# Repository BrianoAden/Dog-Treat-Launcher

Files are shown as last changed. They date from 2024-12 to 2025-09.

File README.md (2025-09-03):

<h1>Dog Treat Dispenser</h1>
<p> This project was for my EDES 301 class. Following is a link to the Hackster.io page I put up detailing the physical build of my project.</p>
<a href="https://www.hackster.io/aden-briano/edes301-dog-treat-launcher-bcfb15">Dog Treat Launcher</a>
<p> Now, I will walk you through the software build required to run this project!</p> 

<h2> Setup </h2>
<p> You are going to need to install the operating system on your PocketBeagle. You will need an SD card and SD card flashing software, like Etcher. 
Download bone-debian-10.11-iot-armhf-2022-02-03-4gb.img.xz from <a href="https://rcn-ee.com/rootfs/bb.org/testing/2022-02-03/buster-iot/">OS</a>. 
Use Etcher to flash your SD card. You can now insert your SD card into your PocketBeagle and plug your PocketBeagle into your laptop. 
Great! Now we can get started. You will need to use the Cloud9 IDE to code on the PocketBeagle using Python. Navigate to http://192.168.6.2:3000/ 
in your browser if you're on mac, or http://192.168.7.2:3000/ if you're on windows. You will also need your Beagle to be connected to the internet for this project. 
There are online resources on how to do this, so I won't walk through it. Once you're on Cloud9, run the following commands.</p>
<p>
                                            $ sudo apt-get update <br>
                                            $ sudo apt-get install build-essential python-dev python-setuptools python-smbus -y <br>
                                            $ sudo apt-get install python-pip python3-pip -y <br>
                                            $ sudo apt-get install zip -y <br>
                                            $ sudo pip3 install --upgrade setuptools <br>
                                            $ sudo pip3 install --upgrade Adafruit_BBIO <br>
                                            $ sudo pip3 install adafruit-blinka <br>
</p>
<p>
Now copy this github repo onto your PocketBeagle using the following command <br>
                                            $ git clone https://github.com/BrianoAden/EDES301 <br>
<h2> Package Installation </h2>
In order to run our project, we need to install the following packages: SpeechRecognition, PyAudio. <br> Let's begin the installation process. Run the following commands. <br>
<br>
$ sudo apt-get update <br>
$ sudo apt-get install -y swig libpulse-dev libasound2-dev <br>
$ sudo apt-get install libportaudio0 libportaudio2 libportaudiocpp0 portaudio19-dev <br>
$ sudo apt-get python-dev <br>
$ sudo python pyaudio/setup.py install <br>
$ sudo python3 -m pip install SpeechRecognition==3.9.0 <br>
<br>

Plug in your USB microphone. Let's check if it's recognized by the PocketBeagle. Run the following command. <br>
$ arecord -l <br>
You should see the following in your output. <br>
<br>
card 1: Device [USB PnP Sound Device], device 0: USB Audio [USB Audio] <br>
  Subdevices: 1/1 <br>
  Subdevice #0: subdevice #0 <br>
<br>
Good, our microphone is almost ready! We just need to set it as our default device. Run the following command. <br>
<br>
$ nano ~/.asoundrc <br>
<br>
Now write in the following. <br>

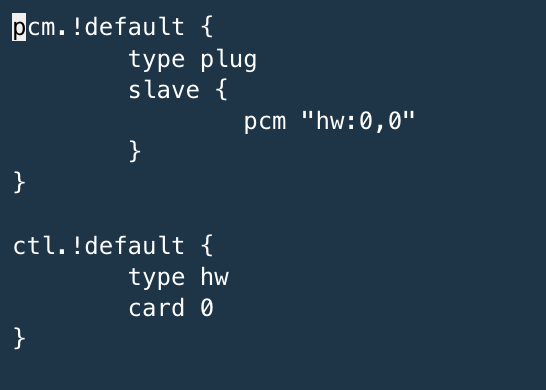
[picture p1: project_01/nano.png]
nano image
 <br>

Redundancy is resiliency, so run this just to be safe. <br>
$ sudo apt-get install -y python-pyaudio python3-pyaudio <br>

Now we should be good to go!
</p>
<h2> Software Operation </h2>
Note! You are required to be connected to the internet to run this project, as the recognize_google() method used by SpeechRecognition requires the internet.
If you manage to connect to the internet through your laptop, but when you reboot your PocketBeagle it disconnects, try running the following commands. <br>
<br>
$ sudo dhclient usb1 <br>
<br>
It's going to ask for a password. The password is temppwd. <br>
If you want to run the program, type sudo ./run into your terminal while in the treat_launcher directory. If this doesn't work, run chmod 755 ./run
to make it executable. To auto-run on boot, perform the following. <br>
<br>
$ sudo crontab -e <br>
<br>
Write the following at the bottom of the file <br>
<br>
@reboot sleep 30 && bash /var/lib/cloud9/EDES301/project_01/python/treat_launcher/run > /var/lib/cloud9/logs/cronlog 2>&1<br>
<br>
Now reboot and it should be good! Run the following to kill the processes. <br>
<br>
$ ps -ef <br>
$ sudo kill -9 (process id(s)) <br>
<br>
Now, you should be set to run the project. In each file under EDES301/project_01/python, there are tests you can use to debug a component.
I hope everything goes well, and I hope your dog loves it! Good luck building!

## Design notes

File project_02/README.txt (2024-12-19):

Dog Treat Launcher PCB

You want to manufacture this PCB??? Wow you must really love your dog! Or you're just curious and wanted to read this file. Well, in the folder that you found this README inside, "project_02", there are three folders. Inside docs are just some screenshots of different parts of the board. Inside EAGLE, you will find the library I used to create the board, as well as the board's schematic and brd file. Inside MFG are the gerber files that you can use if you feel like spending a pretty penny on manufacturing this board. 
This board is designed after the Dog Treat Launcher I designed and developed in project_01. If you care to learn more about that project, please read the README file in project_01. Following is the link to the hackster page I put up for the project. https://www.hackster.io/aden-briano/edes301-dog-treat-launcher-bcfb15 Enjoy!

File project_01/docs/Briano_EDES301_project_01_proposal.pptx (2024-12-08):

## EDES 301 Dog Treat Dispenser

12/05/2024
Aden Briano

## Background Information

  - Inspiration: Dog Treat Dispenser W/Arduino (https://www.sciencebuddies.org/science-fair-projects/project-ideas/Elec_p106/electricity-electronics/automatic-dog-treat-dispenser)
  - Packages to use: Adafruit_BBIO (https://pypi.org/project/Adafruit-BBIO/), SpeechRecognition (https://github.com/Uberi/speech_recognition/blob/master/reference/library-reference.rst), PyAudio (https://github.com/CristiFati/pyaudio)
Is your dog tired of having to sit or lie down to receive a treat? Do they want something more stimulating? Well I’ve got them covered! I’m going to make a treat dispenser box with a flywheel launcher and treat feeder mechanism lying on top. In front of the box there will be a large blue button and a large yellow button with a same colored LED above, embedded into the wall of the box. When the human gives the “Start the game” command, a random LED will light up, and the dog is required to press the corresponding button in 10 seconds to launch a treat (which they can then chase after). The box will need to receive the command again to restart the process. The Dispenser will use an IR sensor to detect if the feeding tube is out of treats, and buzz loudly when it needs to be refilled.

## Github Repository and Hackster.io Post

Dog Treat Launcher (https://www.hackster.io/aden-briano/edes301-dog-treat-launcher-bcfb15)
EDES301 Github (https://github.com/BrianoAden/EDES301)

## System Block Diagram

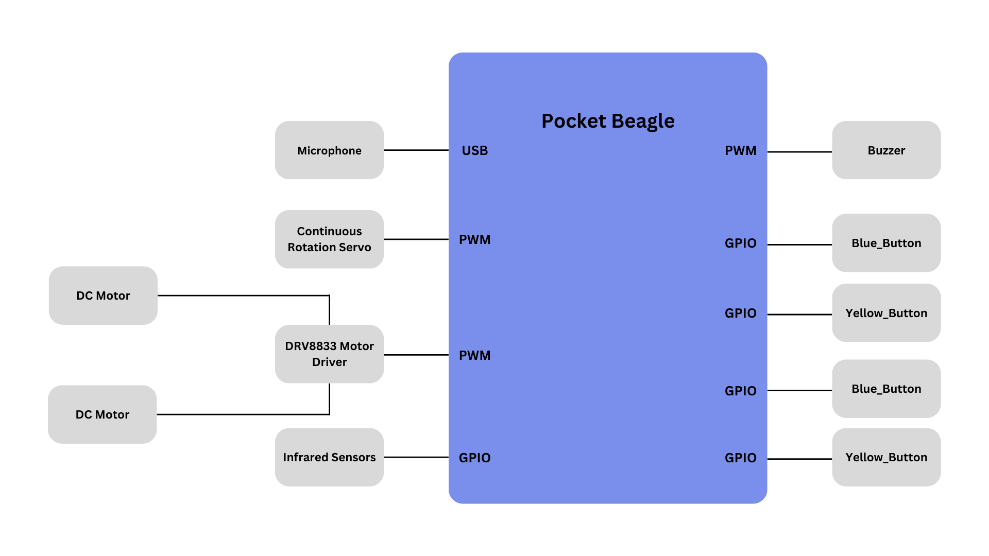
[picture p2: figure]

## Power Block Diagram

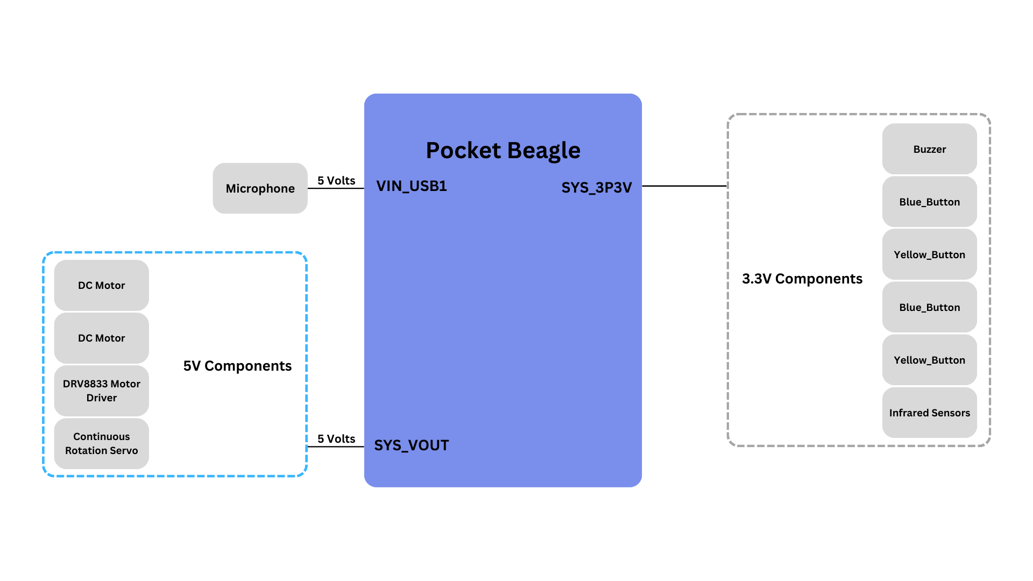
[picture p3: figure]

## Software Framework Diagram

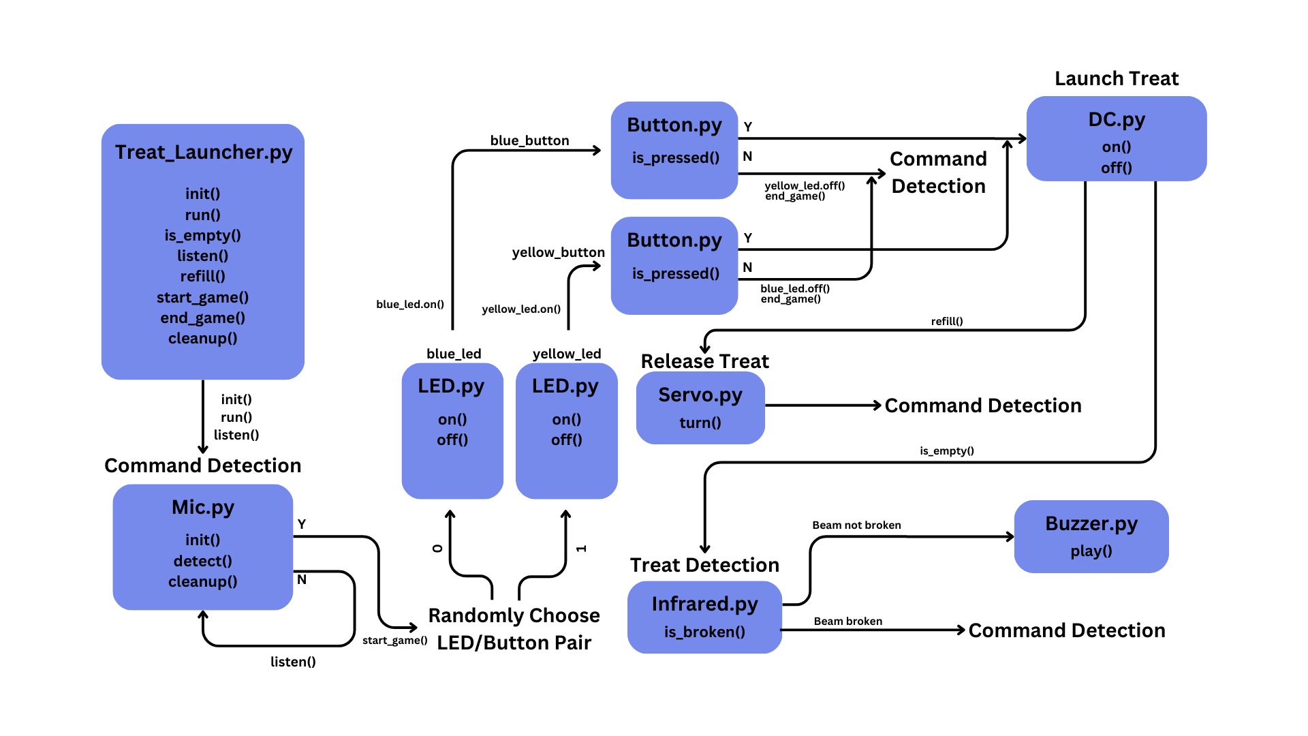
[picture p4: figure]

## Components / Budget

Component | EDES301 to Buy? | Cost
Continuous Rotation Motors (https://www.amazon.com/FEETECH-Continuous-Rotation-Matching-Helicopter/dp/B0B42KLJ9G?th=1) | Yes | $26.99
L298N Motor Driver (https://www.amazon.com/Qunqi-Controller-Module-Stepper-Arduino/dp/B014KMHSW6) | Yes | $6.99
Blue and Yellow Button (https://www.adafruit.com/product/1186) | No | $20
USB Microphone (https://www.amazon.com/gp/product/B01MQ2AA0X) | No | $7.96
Buzzer | No | N/A
DC Motors (https://www.amazon.com/EUDAX-Electric-Magnetic-Propeller-Connector/dp/B08GPPJR1T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) | No | $11.99
Rigid Clear Acrylic Pipe (https://www.amazon.com/MECCANIXITY-Acrylic-Lanterns-Cooling-System/dp/B0B6QFJCLZ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) | No | $14.14
IR Sensor (https://www.electromaker.io/shop/product/ir-break-beam-sensor-3mm-leds?gad_source=1) | No | $9.99
Yellow and Blue LEDS | No | N/A

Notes: Need DC motors for flywheel mechanism. Continuous rotation servo for feeding mechanism.

How do I know when the treats are empty? How will I alert the user?
When do I stop dispensing treats?
Finalize BOM

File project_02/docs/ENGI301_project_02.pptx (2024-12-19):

## EDES 301 PCB Project

Aden Briano
Due 12/17/2024 @ 11:59pm

## Project Options

- Can choose one of two options:
  1. Create a PCB based on your Project #1
  2. Create a PCB based on an example project
- See Project #2 assignment for specific details
  - If choosing Option 1
    - Replace Background Information and System Block Diagram slides with your slides from the Project #1 proposal
    - Create a Mechanical Drawing
  - If choosing Option 2
    - Used provided Background Information and System Block Diagram slides
    - Create a Mechanical Drawing

Remove this slide in your submission

## Background Information

- Hardware:
  - Two DC Motors
  - SG90 Servo
  - IR Break Beam Sensor
  - Two Buttons and Two LEDS (Blue, Yellow)
  - USB Microphone
  - Buzzer
- Software:
  - Adafruit_BBIO (https://pypi.org/project/Adafruit-BBIO/)
  - SpeechRecognition (https://github.com/Uberi/speech_recognition/blob/master/reference/library-reference.rst)
  - PyAudio (https://github.com/CristiFati/pyaudio)

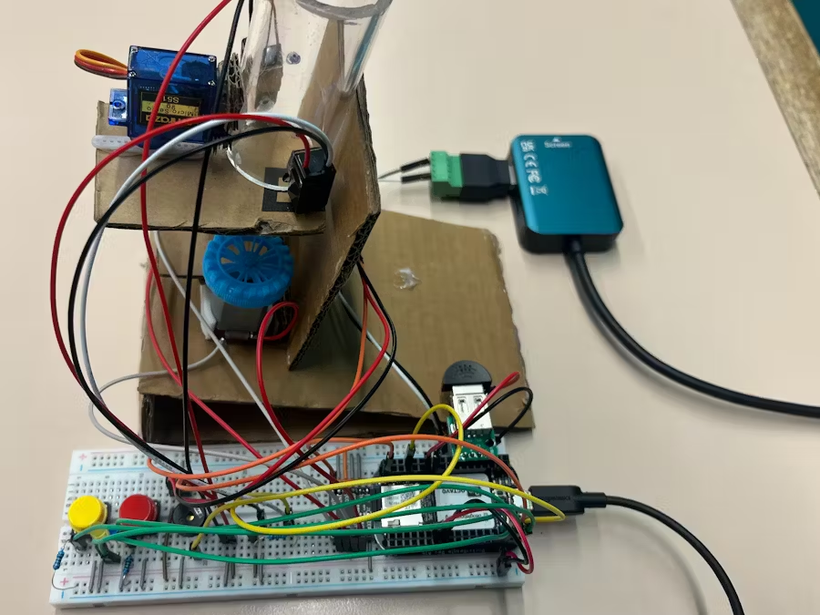
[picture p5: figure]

## System Block Diagram – Dog Treat Launcher

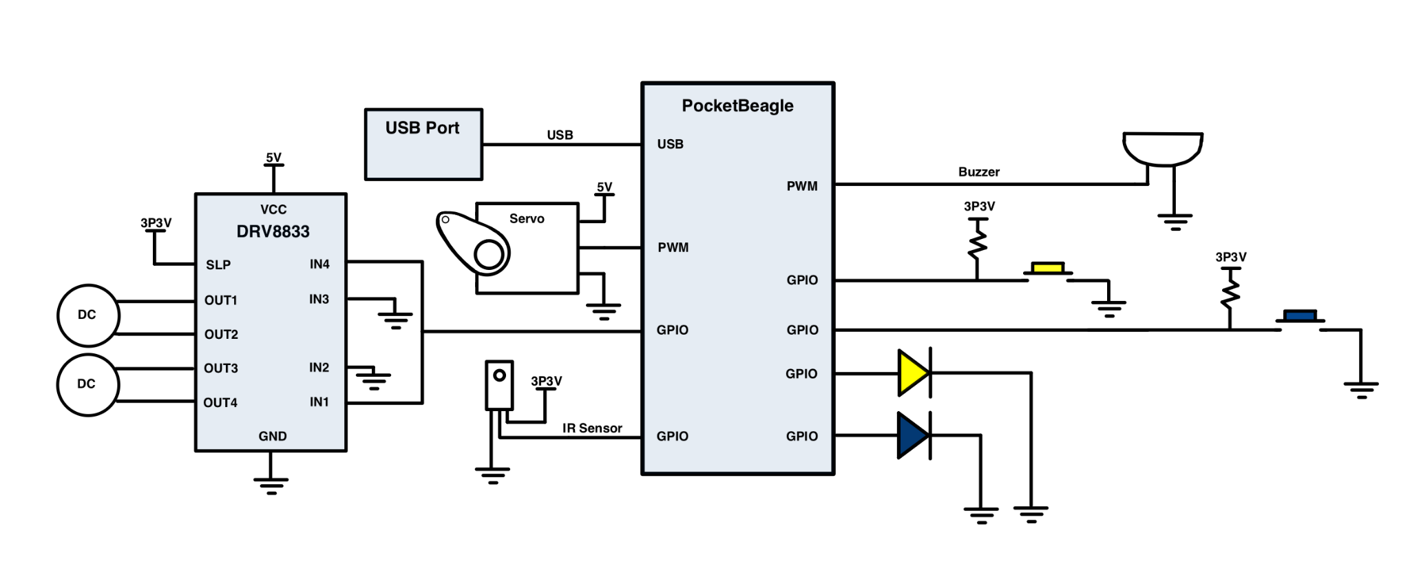
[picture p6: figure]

## Mechanical Drawing

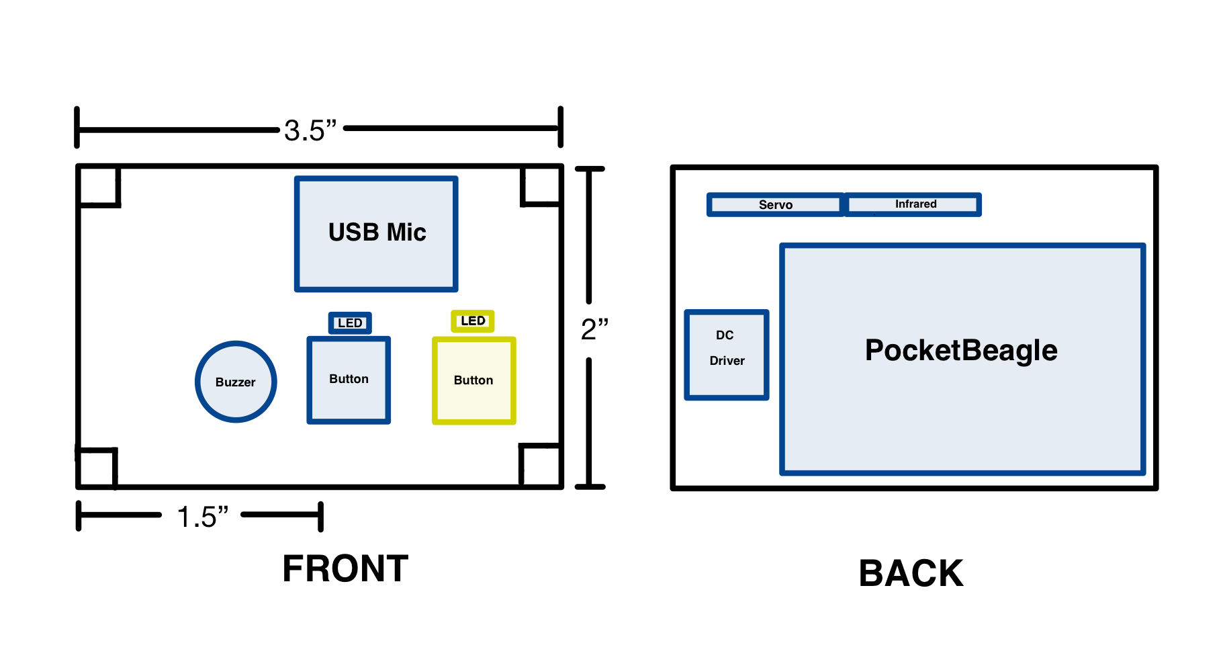
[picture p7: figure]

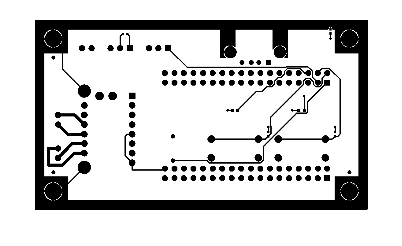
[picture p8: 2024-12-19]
project_02/docs/Top_Layer_Photos/Top_Copper.png

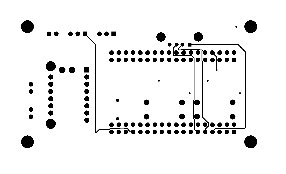
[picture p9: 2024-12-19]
project_02/docs/Bottom_Layer_Photos/Bottom_Copper.png

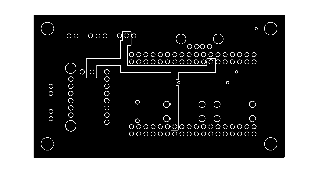
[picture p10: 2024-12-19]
project_02/docs/Top_Layer_Photos/Copper_Layer_15.png

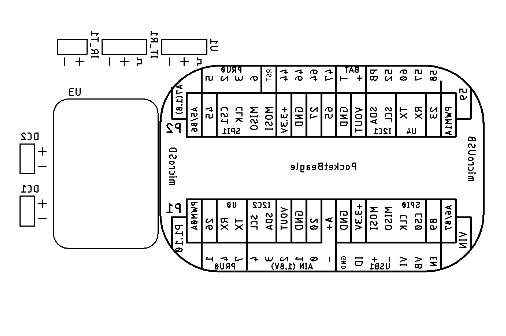
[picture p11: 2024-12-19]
project_02/docs/Bottom_Layer_Photos/Silkscreen_Bottom.png

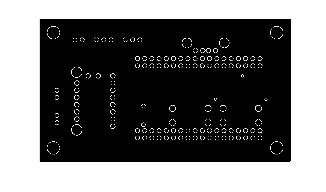
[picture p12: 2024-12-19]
project_02/docs/Top_Layer_Photos/Copper_Layer_2.png

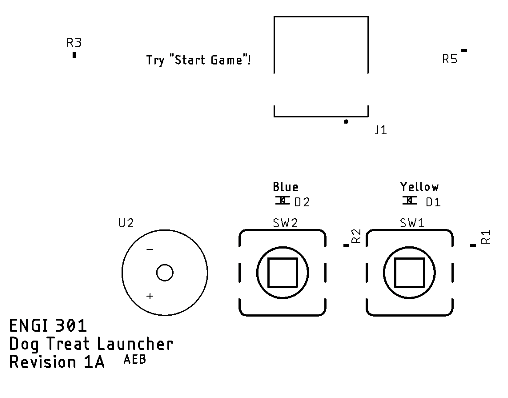
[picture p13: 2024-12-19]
project_02/docs/Top_Layer_Photos/Silkscreen_Top.png

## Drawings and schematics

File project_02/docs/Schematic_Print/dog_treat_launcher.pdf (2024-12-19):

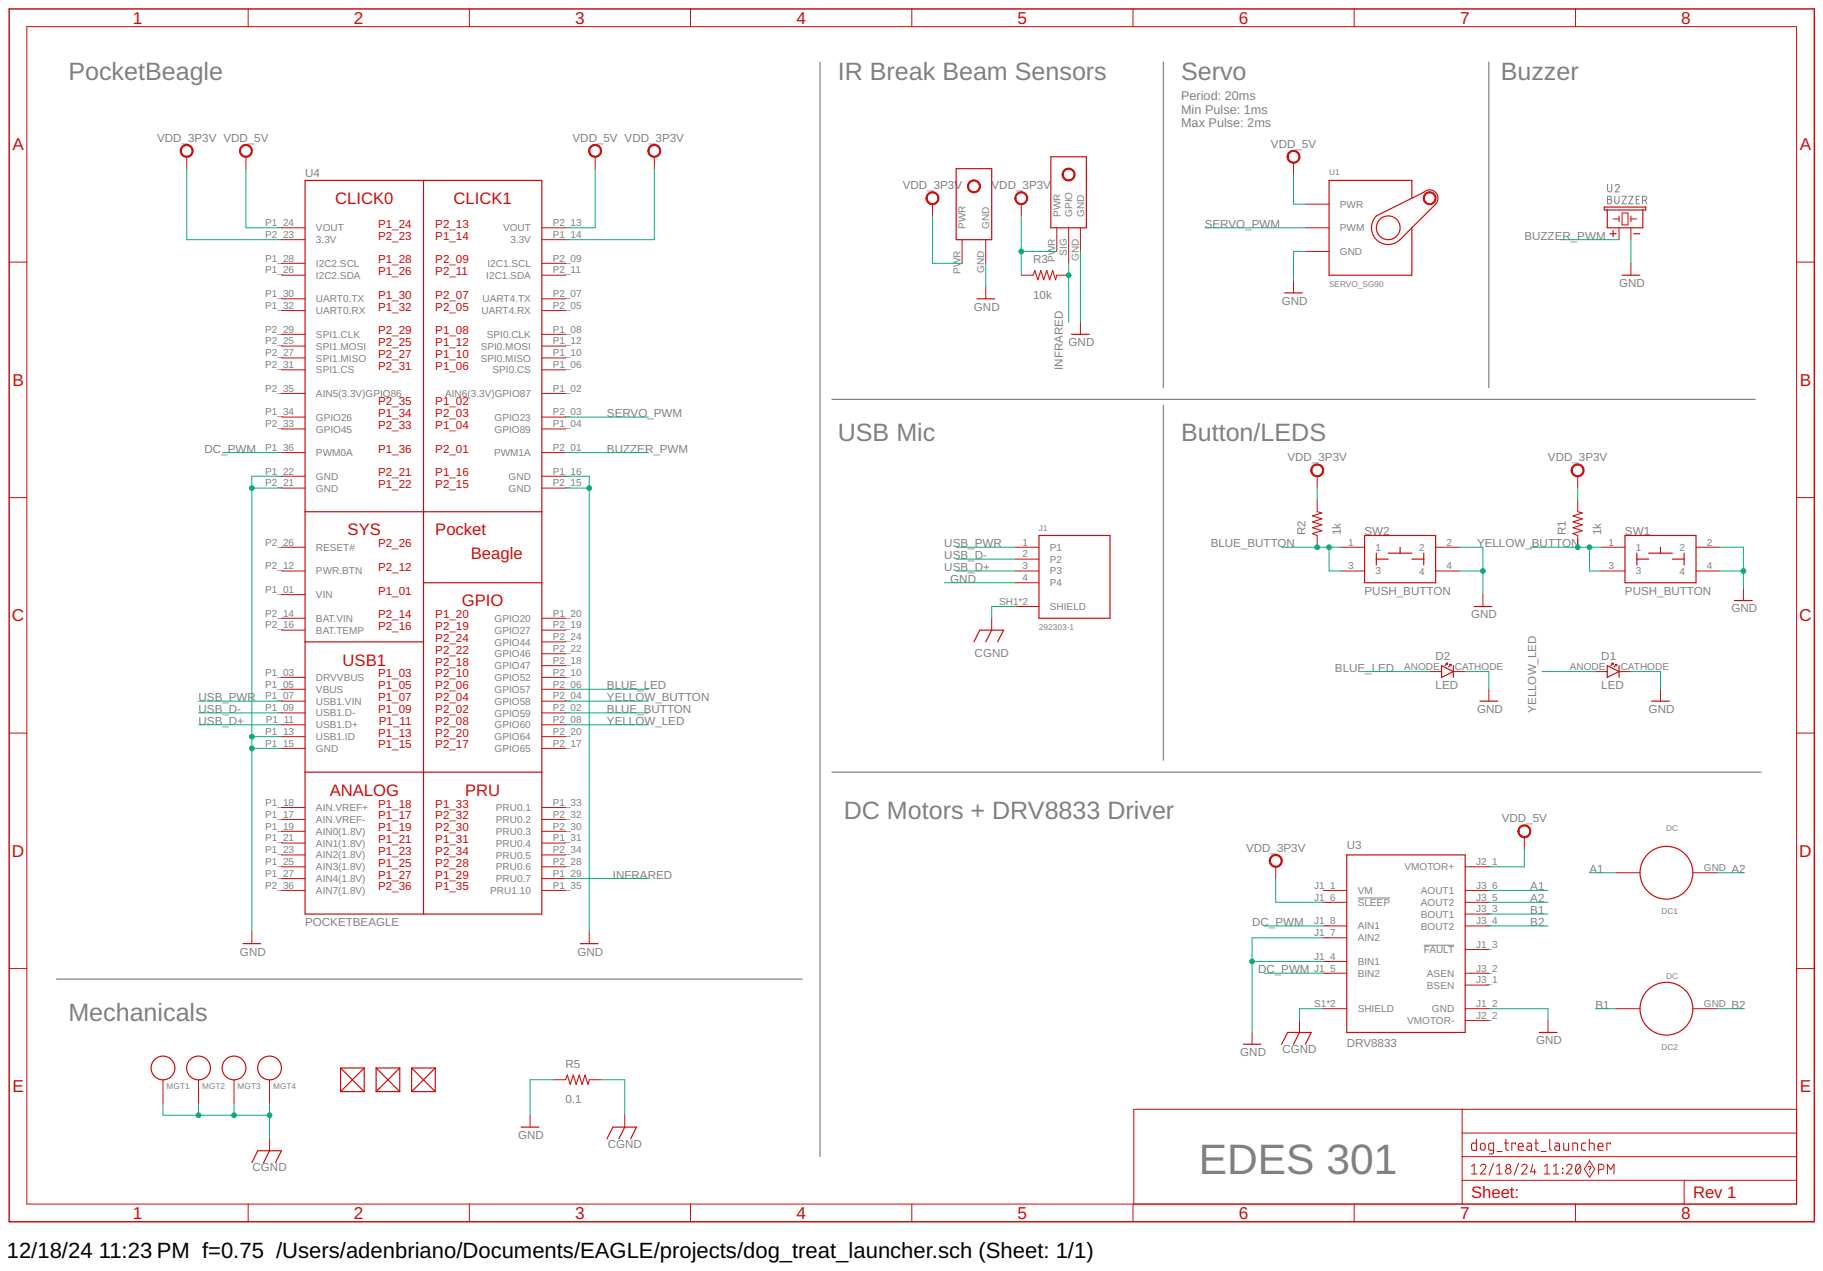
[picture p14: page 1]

Buzzer Period: 20ms Min Pulse: 1ms Max Pulse: 2ms

PWR GND GND GPIO

EDES 301

Sheet: | Rev 1

12/18/24 11:23 PM f=0.75 /Users/adenbriano/Documents/EAGLE/projects/dog_treat_launcher.sch (Sheet: 1/1)

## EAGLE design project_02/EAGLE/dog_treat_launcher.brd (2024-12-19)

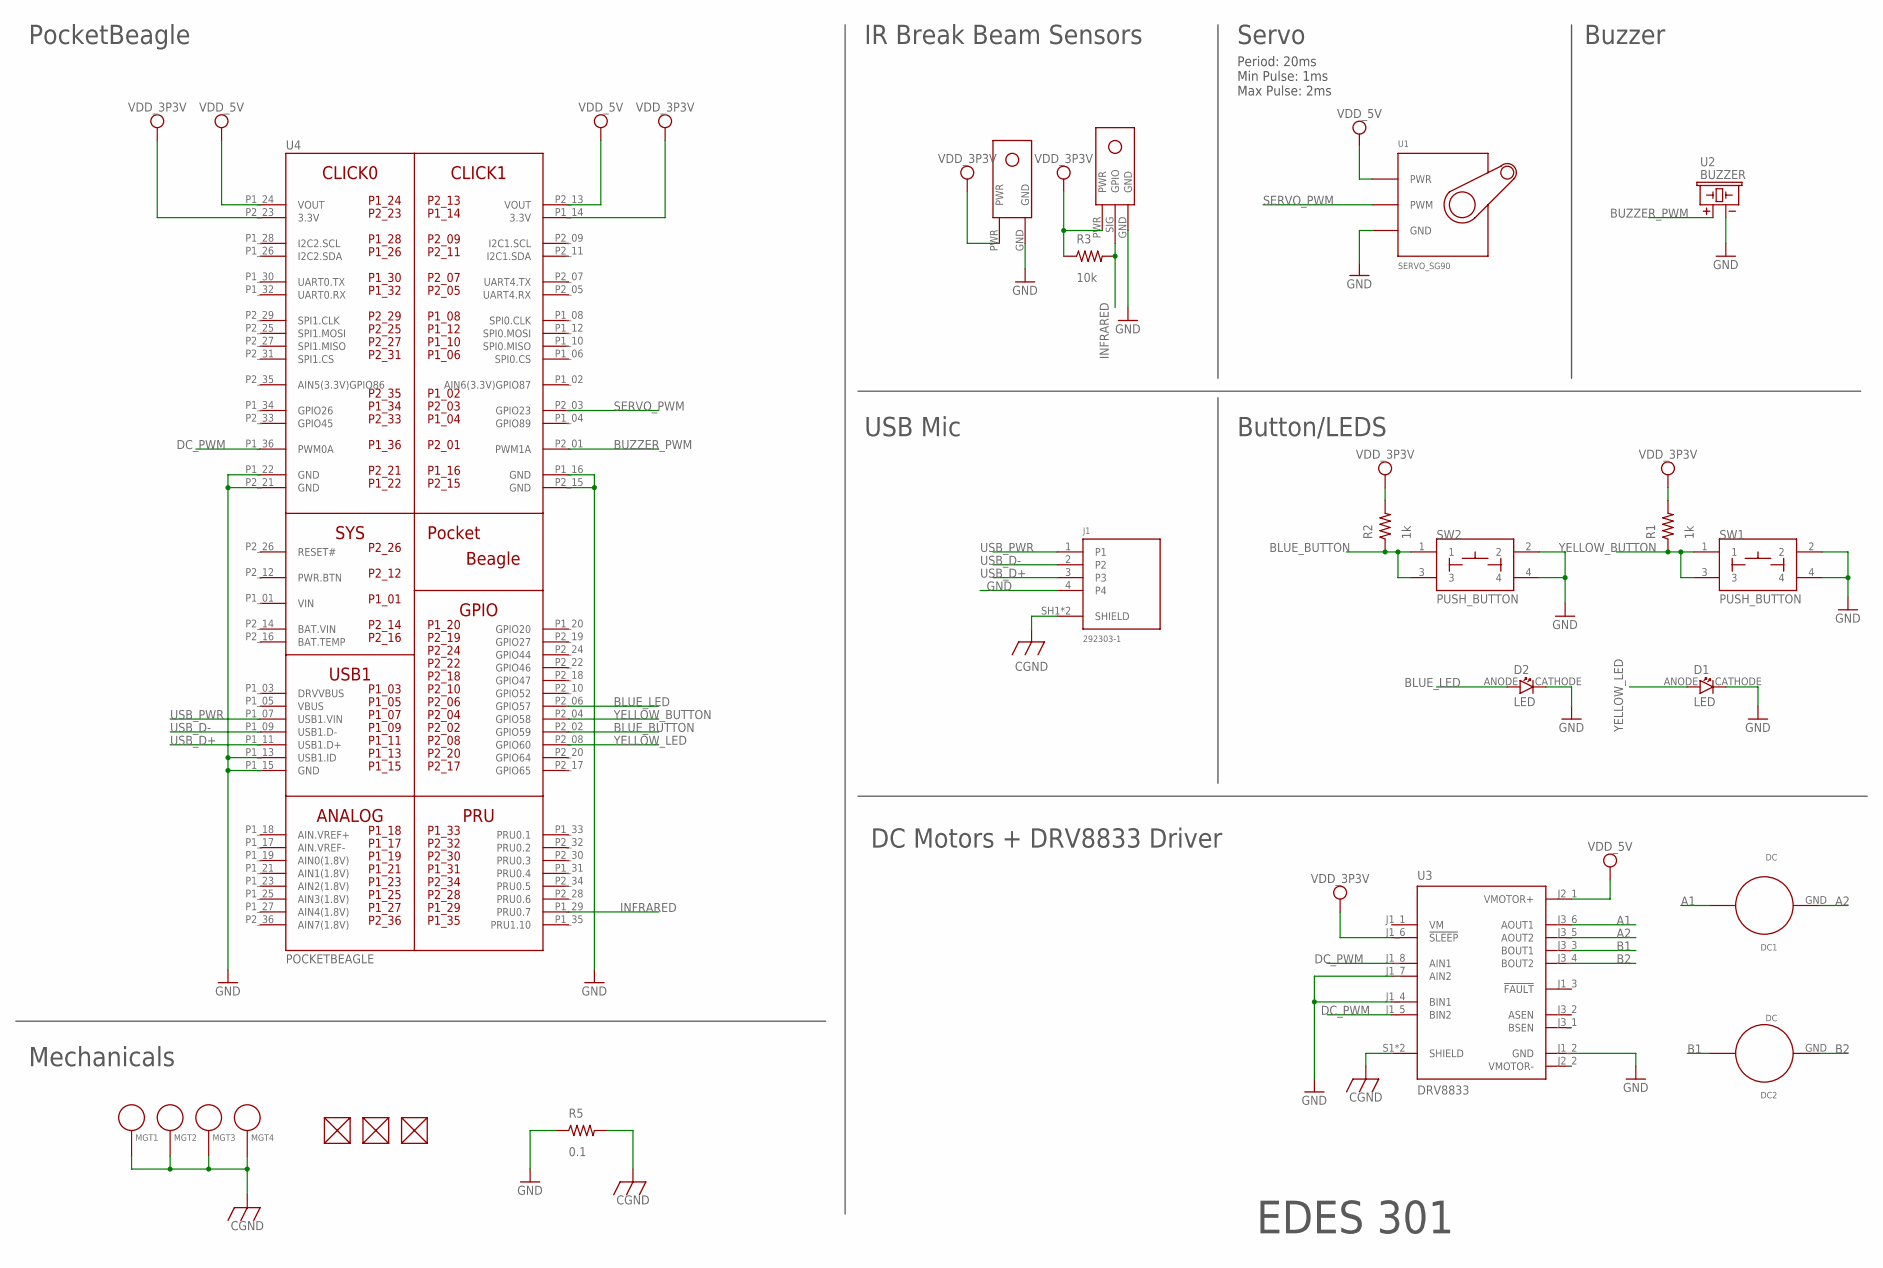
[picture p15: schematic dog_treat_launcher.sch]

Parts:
D1, D2: LED; EIA-STD
DC1, DC2: DC; DC_FOOTPRINT
FUD1, FUD2, FUD3: FIDUCIAL; FIDUCIAL_40MIL
IR_T1: IR_TRANSMITTER; IR_T
IT_R1: IR_RECIEVER; IR_R
J1: 292303-1; TE_292303-1
MGT1, MGT2, MGT3, MGT4: MOUNTING_HOLE
R1, R2: 1k; R0402
R3: 10k; R0402
R5: 0.1; R0402
SW1, SW2: PUSH_BUTTON; BUTTON_12.5MM
U1: SERVO_SG90; SERVO-X1
U2: BUZZER; BUZZER_6.5MM
U3: DRV8833; MODULE_3297
U4: POCKETBEAGLE

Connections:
A1: DC1.PWR, U3.J3_6 (AOUT1)
A2: DC1.GND, U3.J3_5 (AOUT2)
B1: DC2.PWR, U3.J3_3 (BOUT1)
B2: DC2.GND, U3.J3_4 (BOUT2)
BAT.VIN: U4.P2_14 (BAT.VIN)
BLUE_BUTTON: R2.1, SW2.1, SW2.3, U4.P2_02 (GPIO59)
BLUE_LED: D2.ANODE, U4.P2_06 (GPIO57)
BUZZER_PWM: U2.+, U4.P2_01 (PWM1A)
CGND: J1.SH1 (SHIELD), J1.SH2 (SHIELD), MGT1.P$1, MGT2.P$1, MGT3.P$1, MGT4.P$1, R5.2, U3.S1 (SHIELD), U3.S2 (SHIELD)
DC_PWM: U3.J1_5 (BIN2), U3.J1_8 (AIN1), U4.P1_36 (PWM0A)
GND: D1.CATHODE, D2.CATHODE, IR_T1.GND, IT_R1.GND, J1.4, R5.1, SW1.2, SW1.4, SW2.2, SW2.4, U1.GND, U2.-, U3.J1_2 (GND), U3.J1_4 (BIN1), U3.J1_7 (AIN2), U4.P1_13 (USB1.ID), U4.P1_15 (GND), U4.P1_16 (GND), U4.P1_22 (GND), U4.P2_15 (GND), U4.P2_21 (GND)
INFRARED: IT_R1.SIG (GPIO), R3.2, U4.P1_29 (PRU0.7)
SERVO_PWM: U1.SIG (PWM), U4.P2_03 (GPIO23)
USB_D+: J1.3, U4.P1_11 (USB1.D+)
USB_D-: J1.2, U4.P1_09 (USB1.D-)
USB_PWR: J1.1, U4.P1_07 (USB1.VIN)
VDD_3P3V: IR_T1.PWR, IT_R1.PWR, R1.2, R2.2, R3.1, U3.J1_6 (!SLEEP), U4.P1_14 (3.3V), U4.P2_23 (3.3V)
VDD_5V: U1.PWR, U3.J2_1 (VMOTOR+), U4.P1_24 (VOUT), U4.P2_13 (VOUT)
VIN: U4.P1_01 (VIN)
VMOTOR-: U3.J2_2 (VMOTOR-)
YELLOW_BUTTON: R1.1, SW1.1, SW1.3, U4.P2_04 (GPIO58)
YELLOW_LED: D1.ANODE, U4.P2_08 (GPIO60)

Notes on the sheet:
PocketBeagle
IR Break Beam Sensors
Servo
Button/LEDS
USB Mic
DC Motors + DRV8833 Driver
Buzzer
Period: 20ms Min Pulse: 1ms Max Pulse: 2ms
EDES 301
Mechanicals

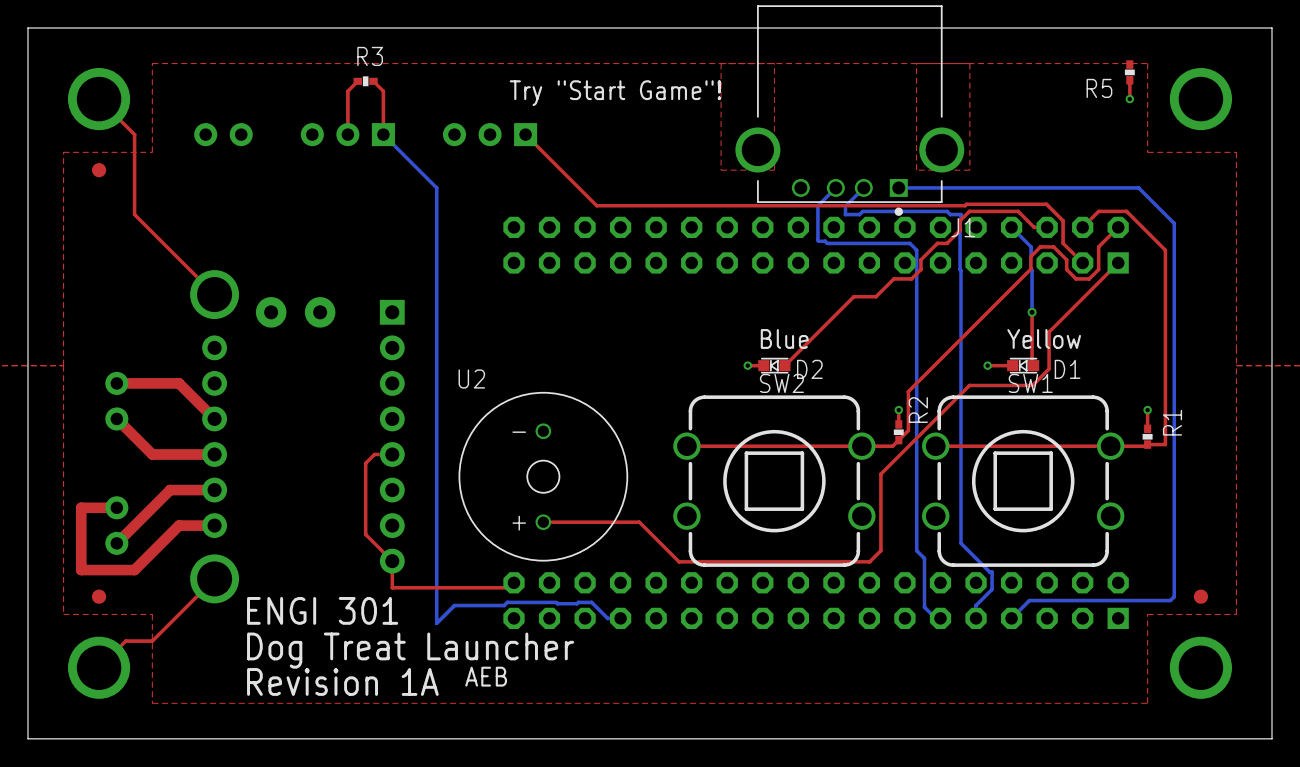
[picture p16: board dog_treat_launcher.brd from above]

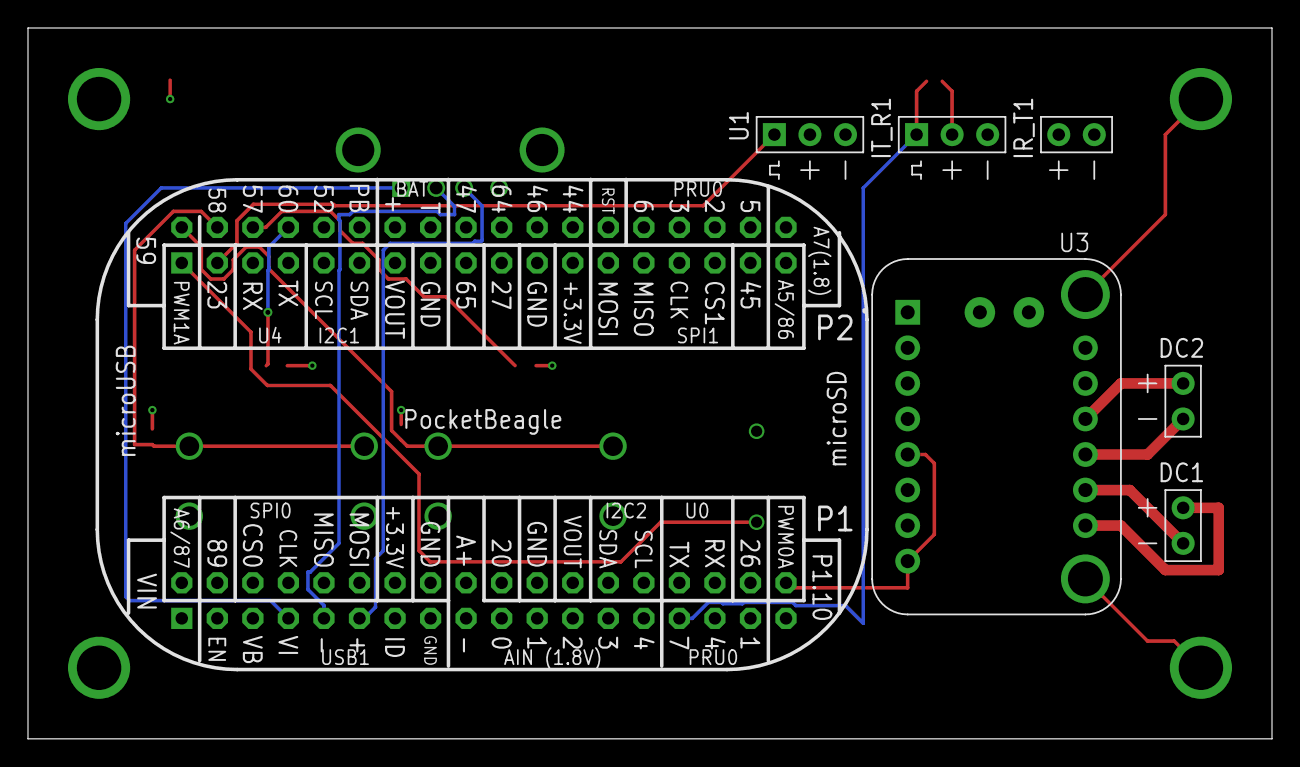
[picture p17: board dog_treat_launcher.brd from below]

Board: 4 copper layers, 88.9 x 50.8 mm, 24 parts (7 on the bottom side), 19 nets.

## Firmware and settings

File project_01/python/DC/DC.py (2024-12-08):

"""
--------------------------------------------------------------------------
DC Motor Driver
--------------------------------------------------------------------------
License:   
Copyright 2024 Aden Briano

Based on library from

Copyright 2024 Erik Welsh

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
1. Redistributions of source code must retain the above copyright notice, this 
list of conditions and the following disclaimer.

2. Redistributions in binary form must reproduce the above copyright notice, 
this list of conditions and the following disclaimer in the documentation 
and/or other materials provided with the distribution.

3. Neither the name of the copyright holder nor the names of its contributors 
may be used to endorse or promote products derived from this software without 
specific prior written permission.

THIS SOFTWARE IS PROVIDED BY THE COPYRIGHT HOLDERS AND CONTRIBUTORS "AS IS" 
AND ANY EXPRESS OR IMPLIED WARRANTIES, INCLUDING, BUT NOT LIMITED TO, THE 
IMPLIED WARRANTIES OF MERCHANTABILITY AND FITNESS FOR A PARTICULAR PURPOSE ARE 
DISCLAIMED. IN NO EVENT SHALL THE COPYRIGHT HOLDER OR CONTRIBUTORS BE LIABLE 
FOR ANY DIRECT, INDIRECT, INCIDENTAL, SPECIAL, EXEMPLARY, OR CONSEQUENTIAL 
DAMAGES (INCLUDING, BUT NOT LIMITED TO, PROCUREMENT OF SUBSTITUTE GOODS OR 
SERVICES; LOSS OF USE, DATA, OR PROFITS; OR BUSINESS INTERRUPTION) HOWEVER 
CAUSED AND ON ANY THEORY OF LIABILITY, WHETHER IN CONTRACT, STRICT LIABILITY, 
OR TORT (INCLUDING NEGLIGENCE OR OTHERWISE) ARISING IN ANY WAY OUT OF THE USE 
OF THIS SOFTWARE, EVEN IF ADVISED OF THE POSSIBILITY OF SUCH DAMAGE.
--------------------------------------------------------------------------

Adafruit hobby DC motor interface

API:
  Servo(pin)
    - Provide pin that the Servo is connected
  
    on()
      -  Turns DC Motor on at MAX_POWER
    off()
      -  Turns DC Motor off. 

"""
import Adafruit_BBIO.PWM as PWM

# ------------------------------------------------------------------------
# Constants
# ------------------------------------------------------------------------

MIN_POWER = 0;
MAX_POWER = 50;

# ------------------------------------------------------------------------
# Global variables
# ------------------------------------------------------------------------

# None

# ------------------------------------------------------------------------
# Functions / Classes
# ------------------------------------------------------------------------

class DCMotor():
    """ Flywheel Launcher """
    
    pin = None
    power = None
    
    def __init__(self, pin=None, default_power=0):
        """ Initialize variables and set up the DCMotor """
        if (pin == None):
            raise ValueError("Pin not provided for DCMotor()")
        else:
            self.pin = pin

        self.power = default_power
        
        self._setup(default_power)
    
    # End def
    
    
    def _setup(self, default_power):
        """Setup the hardware components."""
        # Initialize DCMotor; DCMotor should be "off"
        PWM.start(self.pin, default_power, 1000, 0)
        
    # End def
    
    def off(self):
        """Turns DC Motor off"""
        
        self.power = MIN_POWER
        PWM.set_duty_cycle(self.pin, MIN_POWER)
    
    def get_power(self):
        """ Return the power of the continuous rotation servo """
        return self.power
    
    # End def
    
    def on(self):
        """ 
        Run DC motor at max speed.
        """
        # Record the current power
        self.power = MAX_POWER
        PWM.set_duty_cycle(self.pin, MAX_POWER)
        
    #End def

    def cleanup(self):
        """Cleanup the hardware components."""
        # Stop servo
        PWM.stop(self.pin)
        PWM.cleanup()
        
    # End def

# End class



# ------------------------------------------------------------------------
# Main script
# ------------------------------------------------------------------------

if __name__ == '__main__':
    import time
    
    print("Servo Test")

    # Create instantiation of the servo
    #servo1 = DCMotor("P1_33")
    servo2 = DCMotor("P1_36")

    # Use a Keyboard Interrupt (i.e. "Ctrl-C") to exit the test
    print("Use Ctrl-C to Exit")
    
    try:
        while(1):
            # Turn Servo anti-clockwise
            #servo1.on()
            servo2.on()
            print("Current power = {0}%".format(servo2.get_power()))
            time.sleep(1)
            
            # Turn Servo clockwise
            #servo1.off()
            servo2.off()
            print("Current power = {0}%".format(servo2.get_power()))
            time.sleep(1)
            
            # Stop Servo
            #servo1.on()
            servo2.on()
            print("Current power = {0}%".format(servo2.get_power()))
            time.sleep(1)
        
    except KeyboardInterrupt:
        pass

    # Clean up hardware when exiting
    #servo1.cleanup()
    servo2.cleanup()

    print("Test Complete")

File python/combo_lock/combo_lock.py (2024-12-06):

"""
--------------------------------------------------------------------------
Combination Lock
--------------------------------------------------------------------------
License:   
Copyright 2022 Erik Welsh

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
1. Redistributions of source code must retain the above copyright notice, this 
list of conditions and the following disclaimer.

2. Redistributions in binary form must reproduce the above copyright notice, 
this list of conditions and the following disclaimer in the documentation 
and/or other materials provided with the distribution.

3. Neither the name of the copyright holder nor the names of its contributors 
may be used to endorse or promote products derived from this software without 
specific prior written permission.

THIS SOFTWARE IS PROVIDED BY THE COPYRIGHT HOLDERS AND CONTRIBUTORS "AS IS" 
AND ANY EXPRESS OR IMPLIED WARRANTIES, INCLUDING, BUT NOT LIMITED TO, THE 
IMPLIED WARRANTIES OF MERCHANTABILITY AND FITNESS FOR A PARTICULAR PURPOSE ARE 
DISCLAIMED. IN NO EVENT SHALL THE COPYRIGHT HOLDER OR CONTRIBUTORS BE LIABLE 
FOR ANY DIRECT, INDIRECT, INCIDENTAL, SPECIAL, EXEMPLARY, OR CONSEQUENTIAL 
DAMAGES (INCLUDING, BUT NOT LIMITED TO, PROCUREMENT OF SUBSTITUTE GOODS OR 
SERVICES; LOSS OF USE, DATA, OR PROFITS; OR BUSINESS INTERRUPTION) HOWEVER 
CAUSED AND ON ANY THEORY OF LIABILITY, WHETHER IN CONTRACT, STRICT LIABILITY, 
OR TORT (INCLUDING NEGLIGENCE OR OTHERWISE) ARISING IN ANY WAY OUT OF THE USE 
OF THIS SOFTWARE, EVEN IF ADVISED OF THE POSSIBILITY OF SUCH DAMAGE.
--------------------------------------------------------------------------

Use the following hardware components to make a programmable combination lock:  
  - HT16K33 Display
  - Button
  - Red LED
  - Green LED
  - Potentiometer (analog input)
  - Servo

Requirements:
  - Hardware:
    - When locked:   Red LED is on; Green LED is off; Servo is "closed"; Display is unchanged
    - When unlocked: Red LED is off; Green LED is on; Servo is "open"; Display is "----"
    - Display shows value of potentiometer (raw value of analog input divided by 8)
    - Button
      - Waiting for a button press should allow the display to update (if necessary) and return any values
      - Time the button was pressed should be recorded and returned
    - User interaction:
      - Needs to be able to program the combination for the “lock”
        - Need to be able to input three values for the combination to program or unlock the “lock”
      - Combination lock should lock when done programming and wait for combination input
      - If combination is unsuccessful, the lock should go back to waiting for combination input
      - If combination was successful, the lock should unlock
        - When unlocked, pressing button for less than 2s will re-lock the lock; greater than 2s will allow lock to be re-programmed

Uses:
  - HT16K33 display library developed in class
    - Library updated to add "set_digit_raw()", "set_colon()"

"""
import time

import ht16k33       as HT16K33
import button        as BUTTON
import potentiometer as POT
import servo         as SERVO
import led           as LED
import buzzer_music as BUZZER_MUSIC

# ------------------------------------------------------------------------
# Constants
# ------------------------------------------------------------------------

SERVO_LOCK         = 100     # Fully anti-clockwise
SERVO_UNLOCK       = 0       # Fully clockwise

POT_DIVIDER        = 8       # Divider used to help reduce potentiometer granularity

# ------------------------------------------------------------------------
# Global variables
# ------------------------------------------------------------------------

# None

# ------------------------------------------------------------------------
# Functions / Classes
# ------------------------------------------------------------------------

class CombinationLock():
    """ CombinationLock """
    reset_time     = None
    button         = None
    red_led        = None
    green_led      = None
    potentiometer  = None
    servo          = None
    display        = None
    debug          = None
    buzzer         = None
    
    def __init__(self, reset_time=2.0, button="P2_2", 
                       red_led="P2_6", green_led="P2_4",
                       potentiometer="P1_19", servo="P1_36", 
                       i2c_bus=1, i2c_address=0x70, buzzer = "P2_1", debug=False):
        """ Initialize variables and set up display """

        self.reset_time     = reset_time
        self.button         = BUTTON.Button(button)
        self.red_led        = LED.LED(red_led)
        self.green_led      = LED.LED(green_led)
        self.potentiometer  = POT.Potentiometer(potentiometer)
        self.servo          = SERVO.Servo(servo, default_position=SERVO_LOCK)
        self.display        = HT16K33.HT16K33(i2c_bus, i2c_address)
        self.buzzer         = BUZZER_MUSIC.BuzzerMusic(buzzer)
        self.debug          = debug
        
        self._setup()
    
    # End def
    
    
    def _setup(self):
        """Setup the hardware components."""

        # Initialize Display
        self.set_display_dash()

        # Button / LEDs / Potentiometer / Servo 
        #   - All initialized by libraries when instantiated

    # End def


    def lock(self):
        """Lock the lock:
               - Turn on red LED; Turn off green LED
               - Set servo to closed
        """
        if self.debug:
            print("lock()")
        
        # Set LEDs
        self.red_led.on()
        self.green_led.off()
        # Set servo to "locked"
        self.servo.turn(SERVO_LOCK)
    # End def


    def unlock(self):
        """Unlock the lock.
               - Turn off red LED; Turn on green LED
               - Set servo to open
               - Set display to "----"
        """
        if self.debug:
            print("unlock()")
            
        # Set LEDs
        self.red_led.off()
        self.green_led.on()
        # Set servo to "unlocked"
        self.servo.turn(SERVO_UNLOCK)
        # Set display to dash
        self.set_display_dash
        
        #Play sounds
        self.buzzer.play_song_from_list(1)
    # End def


    def show_analog_value(self):
        """Show the analog value on the screen:
               - Read raw analog value
               - Divide by 4 (remove two LSBs)
               - Display value
               - Return value
        """
        if self.debug:
            print("show_analog_value()")
            
        # Read value from Potentiometer
        value = self.potentiometer.get_value()
        # Divide value by POT_DIVIDER
        value = int(value/ POT_DIVIDER)
        # Update display (must be an integer)
        self.display.update(value)
        # Return value
        return value

    # End def
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

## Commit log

2024-10-23 Added software framework
2024-12-08 fixed file documentation and updated README
    [DC.py, button.py, crs.py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]
2024-12-19 Add project_02
    [dog_treat_launcher.brd, dog_treat_launcher.sch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]
